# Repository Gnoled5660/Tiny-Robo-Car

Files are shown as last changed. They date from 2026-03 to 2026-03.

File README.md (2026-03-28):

# Description
This project is a self autonomous driving car. It is using only a camera sensor to navigate. The idea was to build a car as small as I can, which still has a steering joint, so that it can manouver correctly. 

# Motivation
I have always wanted to build a car with proper steering joints. But I also came up with the idea, to build something tiny. Thats why I decided to build a tiny car. For me this was kind of a new challenge, since I have never made something so small, that I had to worry about space. Through out this project, I have learned to build proper steering joints and also cars in general, which I didn't know how to do before.  

Bildschirmfoto 2026-03-15 um 17 58 01
Bildschirmfoto 2026-03-15 um 14 44 35
Bildschirmfoto 2026-03-21 um 21 50 06



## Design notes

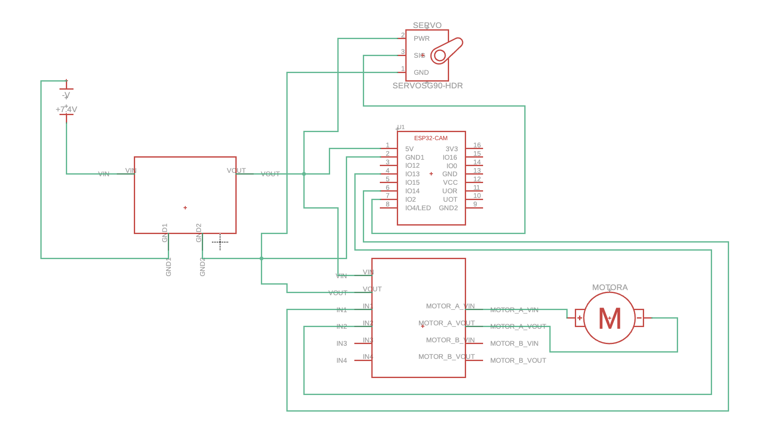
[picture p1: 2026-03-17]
Circuits/schematic.png

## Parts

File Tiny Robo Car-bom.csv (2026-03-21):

Name | Purpose | Quantity | Total Cost (USD) | Link | Distributor
Shipping Fee | Shipping fee | 1 | 5.73 | https:/0 | Roboter-Baustz
3.7V Battery | Battery Energy source | 1 | 0.00 | https://0 | 0
MT3608 | Voltage Converter | 1 | 1.22 | https://www.roboter-bausatz.de/p/spannungswandler-mt3608-dc-dc-step-up-modul-2a-2v-28v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 | Roboter-Baustz
MG90S | Steering | 1 | 5.95 | https://www.roboter-bausatz.de/p/mg90s-micro-servo-motor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 | Roboter-Baustz
NC20 DC Motor | Motor | 1 | 5.04 | https://www.roboter-bausatz.de/p/dc-motor-mit-metallgetriebe-ga12-n20-6v-100-rpm?sPartner=8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 | Roboter-Bausatz
ESP32 CAM Ai thinker | Computer Vision and Computer Processing | 1 | 15.50 | https://www.amazon.de/diymore-Entwicklungsplatine-Entwicklung-Dual-Core-Entwicklungsplatine-Kamera-TF-Karten-Modul/dp/B0F2F24JSZ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 | Amazon
MX1508 | Motor driver | 1 | 0.00 | https://0 | 0

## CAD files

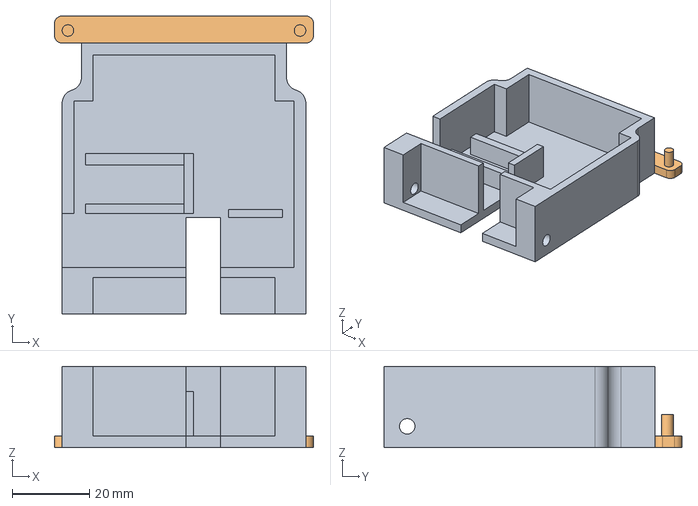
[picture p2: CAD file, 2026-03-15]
CAD/MainBottom.step
67.0 x 77.0 x 21.0 mm

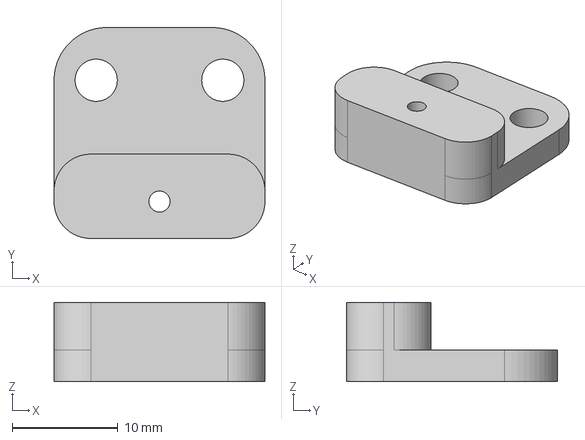
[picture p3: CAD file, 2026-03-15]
CAD/Steering joint/Main Steering Joint.step
20.0 x 20.0 x 7.50 mm

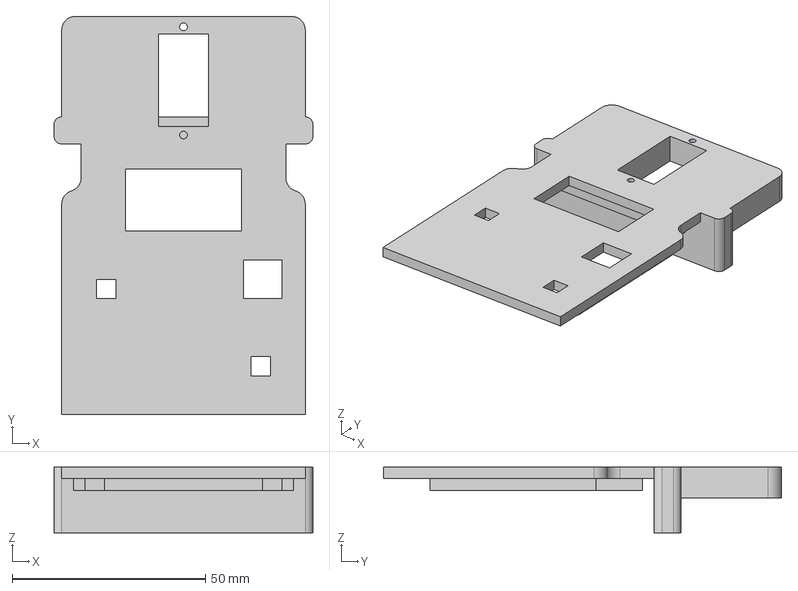
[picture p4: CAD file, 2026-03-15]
CAD/MainTop.step
67.0 x 103.0 x 17.0 mm

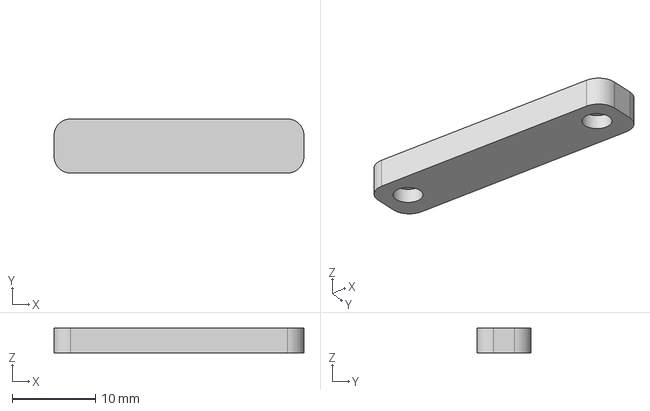
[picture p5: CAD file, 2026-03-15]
CAD/Steering joint/ShortTop1.step
30.0 x 6.50 x 3.00 mm

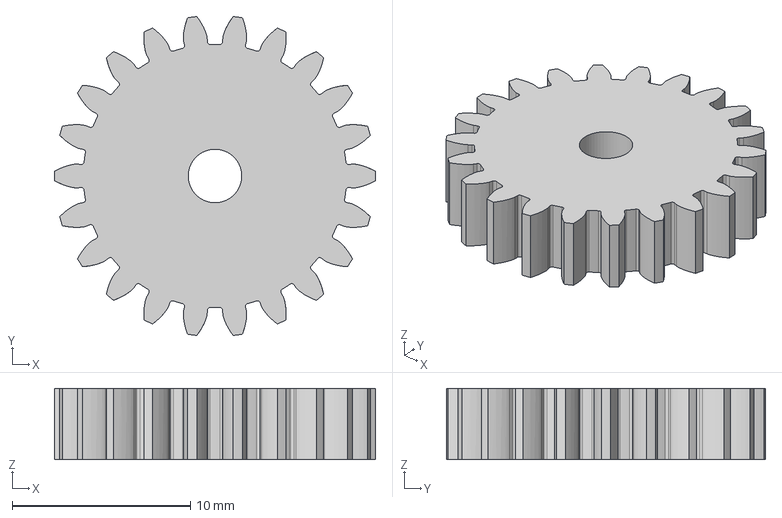
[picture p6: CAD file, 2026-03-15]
CAD/Gear big.step
18.0 x 17.9 x 4.00 mm

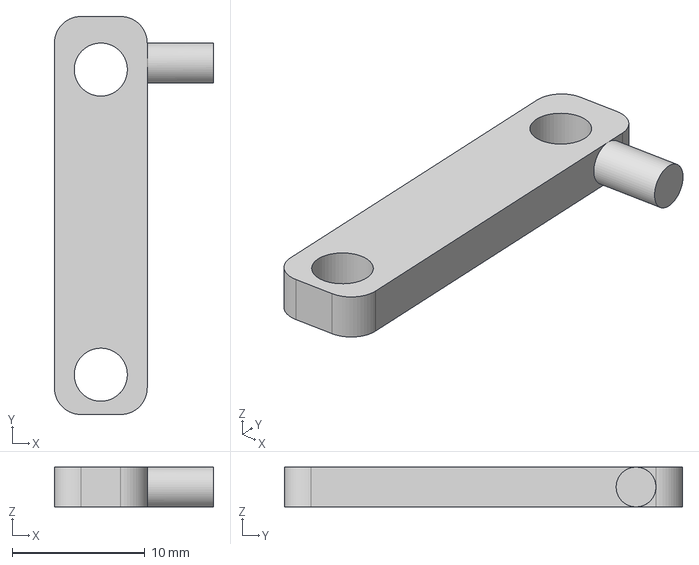
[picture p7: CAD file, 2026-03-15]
CAD/Steering joint/Wheels 1.step
12.0 x 30.0 x 3.00 mm

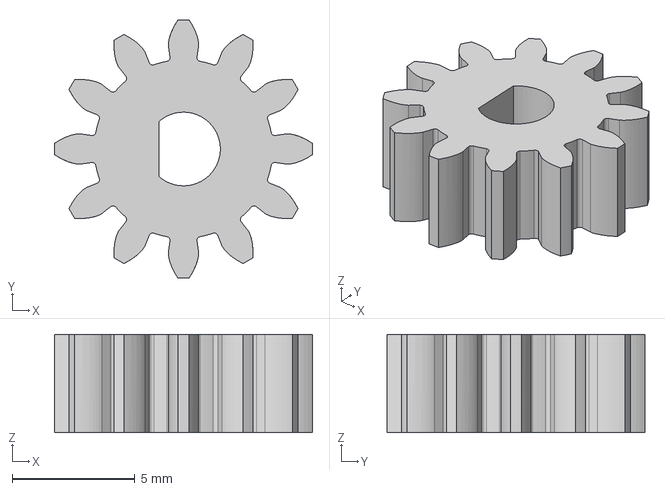
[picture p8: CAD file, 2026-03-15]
CAD/Gear small.step
10.5 x 10.5 x 4.00 mm

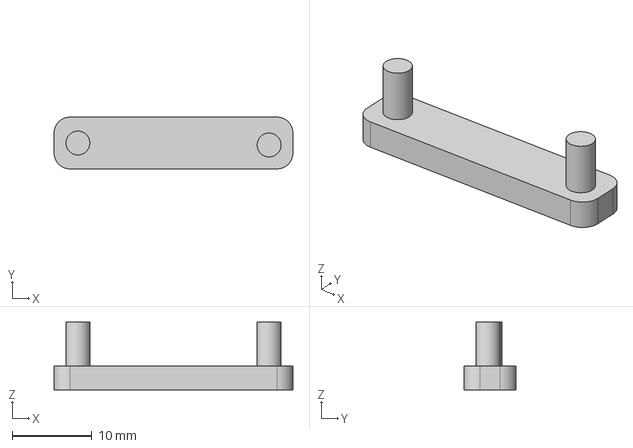
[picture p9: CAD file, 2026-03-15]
CAD/Steering joint/ShortBottom1.step
30.0 x 6.50 x 8.50 mm

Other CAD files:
CAD/Steering joint/ShortBottom2.step
CAD/Steering joint/Wheels 2.step
CAD/Steering joint/ShortTop2.step
CAD/Robo Car.f3d

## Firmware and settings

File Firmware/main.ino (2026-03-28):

#include <ESP32PWM.h>
#include <ESP32Servo.h>
#include <esp_camera.h>

#define PWDN_GPIO_NUM 32
#define RESET_GPIO_NUM -1
#define XCLK_GPIO_NUM 0
#define SIOD_GPIO_NUM 26
#define SIOC_GPIO_NUM 27

#define Y9_GPIO_NUM 35
#define Y8_GPIO_NUM 34
#define Y7_GPIO_NUM 39
#define Y6_GPIO_NUM 36
#define Y5_GPIO_NUM 21
#define Y4_GPIO_NUM 19
#define Y3_GPIO_NUM 18
#define Y2_GPIO_NUM 5
#define VSYNC_GPIO_NUM 25
#define HREF_GPIO_NUM 23
#define PCLK_GPIO_NUM 22

#define Motor_Pin_1 14
#define Motor_Pin_2 13
#define Servo_Pin 2

Servo servo;

int Servo_Value = 350;

void setup() {
  Serial.begin(115200);
  camera_config_t config;
  config.ledc_channel = LEDC_CHANNEL_0;
  config.ledc_timer = LEDC_TIMER_0;
  config.pin_d0 = Y2_GPIO_NUM;
  config.pin_d1 = Y3_GPIO_NUM;
  config.pin_d2 = Y4_GPIO_NUM;
  config.pin_d3 = Y5_GPIO_NUM;
  config.pin_d4 = Y6_GPIO_NUM;
  config.pin_d5 = Y7_GPIO_NUM;
  config.pin_d6 = Y8_GPIO_NUM;
  config.pin_d7 = Y9_GPIO_NUM;
  config.pin_xclk = XCLK_GPIO_NUM;
  config.pin_pclk = PCLK_GPIO_NUM;
  config.pin_vsync = VSYNC_GPIO_NUM;
  config.pin_href = HREF_GPIO_NUM;
  config.pin_sccb_sda = SIOD_GPIO_NUM;
  config.pin_sccb_scl = SIOC_GPIO_NUM;
  config.pin_pwdn = PWDN_GPIO_NUM;
  config.pin_reset = RESET_GPIO_NUM;
  config.xclk_freq_hz = 20000000;

  config.pixel_format = PIXFORMAT_RGB565;
  config.frame_size = FRAMESIZE_QVGA;
  config.jpeg_quality = 12;
  config.fb_count = 1;

  pinMode(Motor_Pin_1, OUTPUT);
  pinMode(Motor_Pin_2, OUTPUT);

  servo.attach(Servo_Pin, 500, 2400);

  servo.write(90);

  esp_err_t err = esp_camera_init(&config);
  if (err != ESP_OK){
    return;
  }

}

void loop() {
  camera_fb_t * fb = esp_camera_fb_get();
  if (!fb){
    Serial.println("Couldn't get an image");
    return;
  }
  int redPixelCount = 0;
  int greenPixelCount = 0;
  int totalPixels = fb->width * fb->height;
  int width = fb->width;
  int height = fb->height;

  int countLeftRed = 0;
  int countCenterRed = 0;
  int countRightRed = 0;

  int countLeftGreen = 0;
  int countCenterGreen = 0;
  int countRightGreen = 0;

  int step =4;

  for (int y = 0; y < height; y += step){
    for (int x = 0; x < width; x += step){
      int index = (y * width + x) * 2;
      uint8_t highByte = fb->buf[index];
      uint8_t lowByte = fb->buf[index+1];

      uint8_t r = (highByte & 0xF8);
      uint8_t g = ((highByte & 0x07) << 5) | ((lowByte & 0xE0) >> 3);
      uint8_t b = (lowByte & 0x1F) << 3;

      if (r < 80 && g < 150 && b < 80){
        greenPixelCount++;
        if (x < width / 3){
          countLeftGreen++;
        }
        else if(x < (width * 2)/3){
          countCenterGreen++;
        }
        else{
          countRightGreen++;
        }
      }
      if (r < 150 && g < 80 && b < 80){
        redPixelCount++;
      }
    }
  }

  int threshold = 10;
  if (greenPixelCount > redPixelCount){
    digitalWrite(Motor_Pin_1, HIGH);
    digitalWrite(Motor_Pin_2, LOW);
    Serial.println(digitalRead(Motor_Pin_1));
    Serial.println(digitalRead(Motor_Pin_2));
    if (countLeftGreen > threshold || countCenterGreen > threshold || countRightGreen > threshold){
      if(countLeftGreen > countCenterGreen && countLeftGreen > countRightGreen){
        servo.write(60);
        Serial.println("GreenLeft");
      }
      else if (countCenterGreen > countLeftGreen && countCenterGreen > countRightGreen){
        servo.write(90);
        Serial.println("GreenCenter");
      }
      else if (countRightGreen > countLeftGreen && countRightGreen > countCenterGreen){
      servo.write(120);
      Serial.println("GreenRight");
      }
    }
  }
  else if(redPixelCount > greenPixelCount && redPixelCount > threshold){
    digitalWrite(Motor_Pin_1, LOW);
    digitalWrite(Motor_Pin_2, LOW);
    servo.write(90);
  }

  else{
    digitalWrite(Motor_Pin_1, LOW);
    digitalWrite(Motor_Pin_2, LOW);
    servo.write(90);
  }
  esp_camera_fb_return(fb);
  delay(50);
}

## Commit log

2026-03-15 Create CAD Files
2026-03-15 Create Schematic
2026-03-15 Create All steering joint files
2026-03-21 Implement camera setup and color-based motor control
    Added camera configuration and motor control logic based on pixel color detection.
2026-03-21 Rename Bildschirmfoto 2026-03-17 um 20.50.05.png to schematic.png
2026-03-28 Fix servo initialization and correct variable names
    [main.ino]
